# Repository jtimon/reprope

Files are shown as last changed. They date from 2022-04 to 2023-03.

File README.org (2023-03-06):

* Reprope

Reprope is a [[https://reprap.org/wiki/RepRap][reprap]] based on ropes or cables.

Cable based robotic designs are very scalable compared to other systems.

Depending on the needs, they can be configured for high precision and torque or high speed.

When it comes to leveraging cable usage for higher torque; Arquímedes himself said it quite clearly:

"Give me a place to stand, and I shall move the earth"

Some people told us Arquímedes once elevated a war ship with his own force
simply by using levers, pulleys, ropes and wooden stuff.

Anyway, it was just a joke, it can be removed with a commit.

* hangprinter

The reprope extends the hangprinter, with a special focus on adding
optional features like scaling it down, allowing squared printing
volumes, allowing extra anchors, allowing extra axes or even getting
use of those extra 3 90 degree axes to get tool chaning without an
extra servo, just rotate the head 90 degrees in 3 directions as you whish.

* Firmware

For now there is only work in progress firmware extending
reprap firmware (RRF) implementation of the hangprinter:

https://github.com/Duet3D/RepRapFirmware/pulls/jtimon

There may be some binaries in bin to test. But they shouldn't be
assumed to work on duet. Most of them will be compiled for the
stm32f4-wifi config on:

https://github.com/gloomyandy/RepRapFirmware

* Copyright

The copyright of this whole project belongs to the RepRope project developers.

The copyright for other free software and hardware projects this
depends on is described in theirr own projects.

This project is intended to be on free software licenses as light as
possible.

I will try to keep dependencies free.
In that sense, the hangprinter and reprap firmware seem to be
following free software licenses practices.

* License

All files included in this project are under MIT license (see [[./COPYING]]),

Currently some stl files used are not included in the project but
references to those files, because they have other licenses.

List of stl files that are used from external developers:

| Part                             | License                         | STL                                             | Notes                                                                                                |
|----------------------------------+---------------------------------+-------------------------------------------------+------------------------------------------------------------------------------------------------------|
| vslot t-nut adaptor for 3mm nuts | Creative Commons Non commercial | https://www.thingiverse.com/thing:3050607/files | You can also just buy regular commercial t-nuts, this is only cheaper if you're not going to sell it |

* NOTE: This is a work in progress, this printer doesn't work yet.

#+CAPTION: This is just the frame with the motors mounted with their reels
#+NAME:   fig:reprope-reels-only
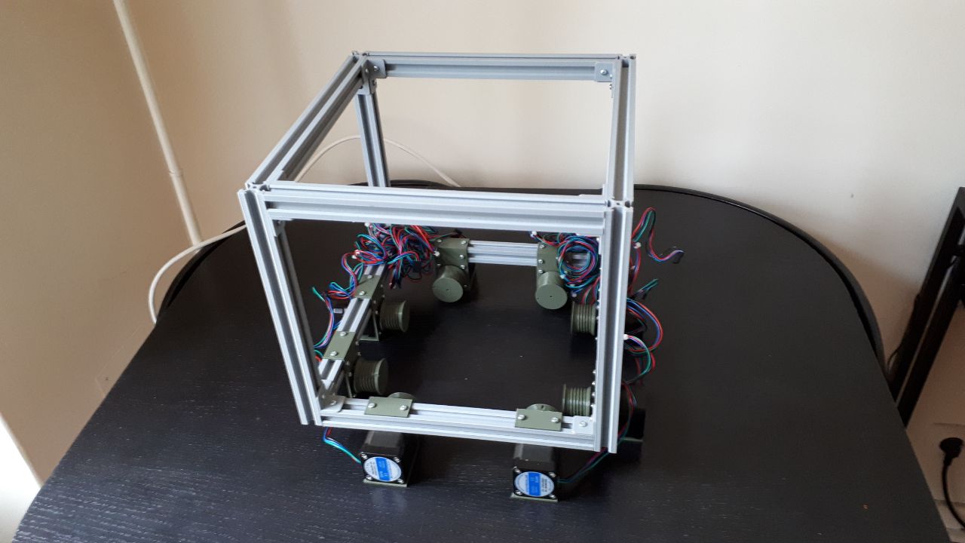
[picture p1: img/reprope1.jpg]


#+CAPTION: This is after adding the top pulleys too
#+NAME:   fig:reprope-pulleys-only
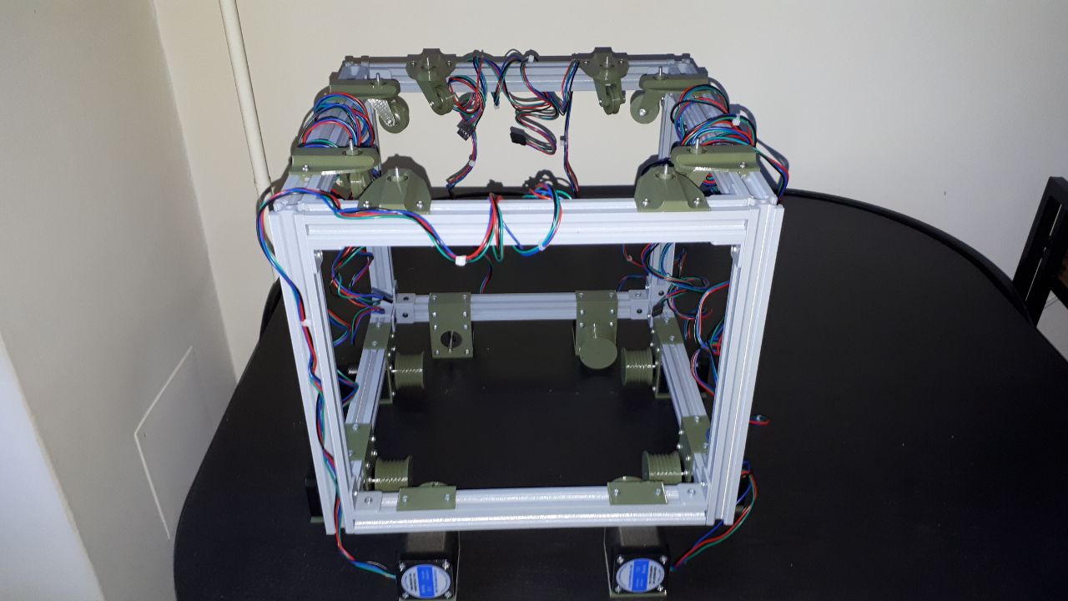
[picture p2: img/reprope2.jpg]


#+CAPTION: This is after adding some nylon ropes
#+NAME:   fig:reprope-blue-ropes
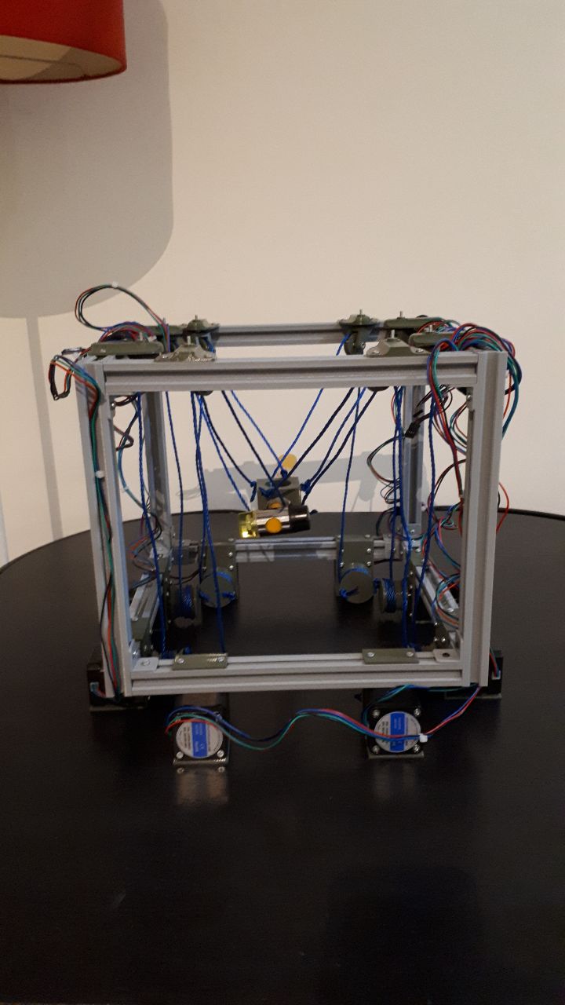
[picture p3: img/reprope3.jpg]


#+NAME:   fig:reprope-blue-ropes2
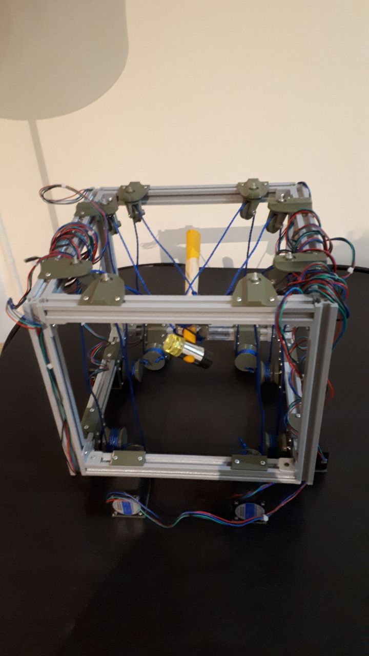
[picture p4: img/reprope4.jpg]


#+NAME:   fig:reprope-blue-ropes3
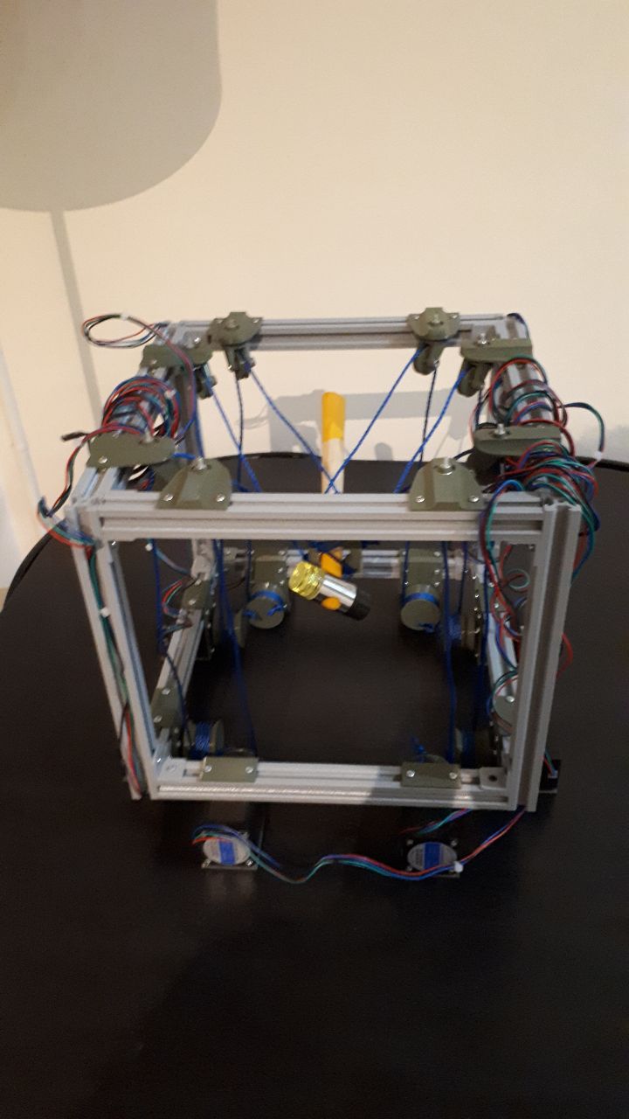
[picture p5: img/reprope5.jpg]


#+NAME:   fig:reprope-psu-box
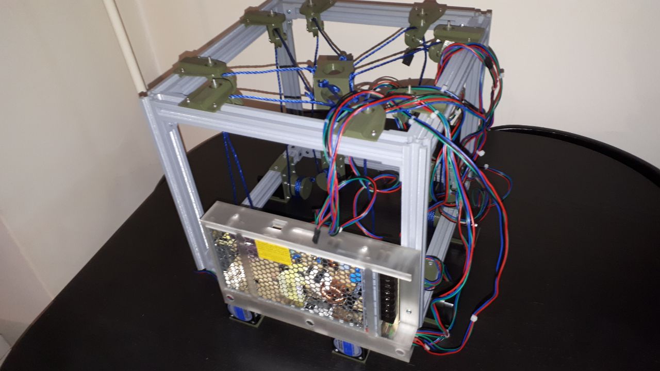
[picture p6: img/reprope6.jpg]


#+NAME:   fig:reprope-psu-box-cable-management
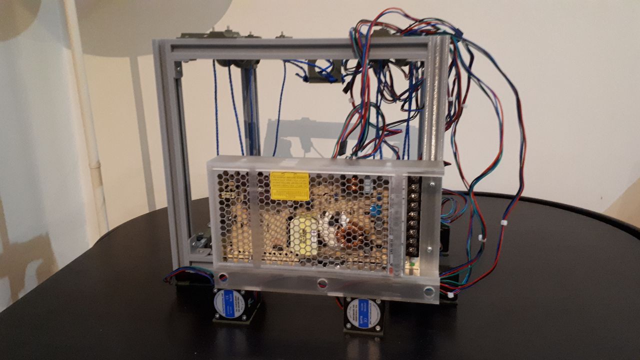
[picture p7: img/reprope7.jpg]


#+NAME:   fig:reprope-ac-in-corner
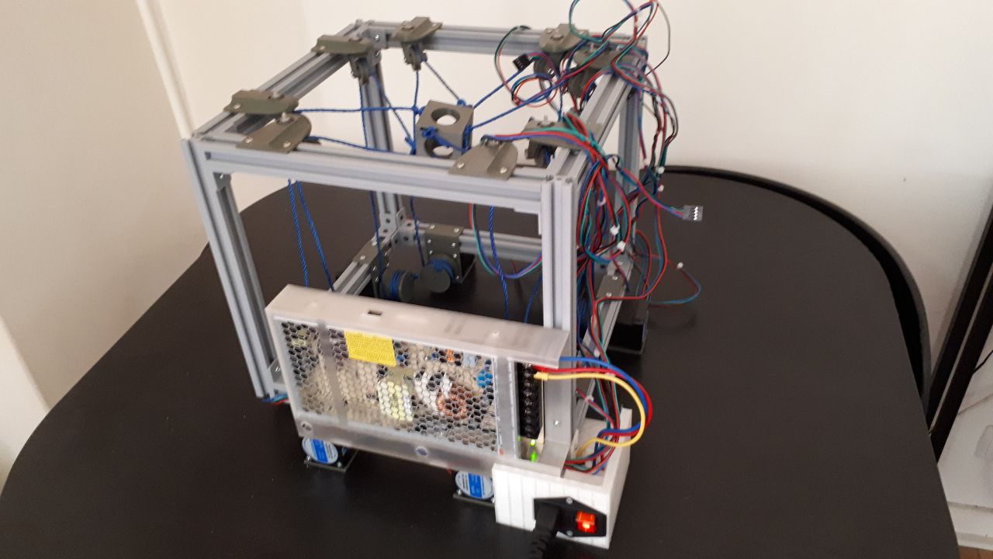
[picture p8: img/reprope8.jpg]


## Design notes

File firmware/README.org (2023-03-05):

* Firmware

Ideally, the reprope kynematics will be eventually supported in all three most popular free software 3d printing firmwares:

- [ ] Reprap firmware (RRF)
- [ ] Klipper
- [ ] Marlin

The plan is to implement, test and pull request them to their original repositories in that order.
A forked branch of the projects will be kept here as submodules and in github/jtimon with their respective names.
Ideally, in the end, a PR will be merged for each of the projects and the submodule can be erased here.

In the case of RRF, since I'm only going to test with non duet hardware for now, I'm not forking the original repository:

https://github.com/Duet3D/RepRapFirmware

but a different one that supports STM32F4 based boards such as the BTT octopus in the current BOM:

https://github.com/gloomyandy/RepRapFirmware

Still, the PR would be to the original repository, and only with the
reprope kynematic specific changes, so there will be a duet-reprope
branch and a stm32-reprope branch. The latter may stay here for a bit
longer until the gloomy version gets the next version including the
new kynematics.

* TODO [0/3] Firmwares
- [ ] Reprap Firmware (RRF)
- [ ] Klipper
- [ ] Marlin

* Why reprap firmware first?

Feel free to beat me to it in klipper.
Marlin I think is going to be harder because of the lack of
polymorphism, at least harder for me.
I may never do it in the case of marlin, quite honestly, but it would
be cool to have the new kynematics in all three.

It can be cheaper per unit using RRF because it doesn't strictly need
a raspbery pi, which are getting harder to get these days.
Besides, that's a whole linux system, many more things can go wrong
with that.

Whatever the order, I really want to do it for both RRF and klipper at
the very least. Sorry, Marlin just seems like too much work, at a glance.
Perhaps it's easier for somebody else who knows it better to port the
new kynematics, once it is done in other firmwares.
No warranties for anything anyway besides whatever gets done being
free software.

Another reason to do RRF first is that I can look at the tested and
working hangprinter kynematics implementation in there.
In my best hopes, once I port the reprope kynematics from RRF to
klipper, I will understand things enough to complete the port of the
hangprinter to klipper, which seems to be:

https://github.com/Klipper3d/klipper/blob/master/klippy/kinematics/winch.py

But, hey, it's well documented that some things are not implemented.

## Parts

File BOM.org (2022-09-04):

#+TODO: TODO WIP CAD PRINT LANG | DONE

* WIP first prototype sourcing

** 3d printed parts

| Part                                        | quantity | State | STL                                                       | CAD                          | Notes                                                                                              |
|---------------------------------------------+----------+-------+-----------------------------------------------------------+------------------------------+----------------------------------------------------------------------------------------------------|
| vslot t-nut adaptor for 3mm nuts (optional) |       77 | DONE  | https://www.thingiverse.com/thing:3050607/files           | MISSING                      | TODO: replace with a CAD parametric one, this one is creative commons but non-commercial           |
| Open builds-inspired 20x20 vslot 26cm       |       12 | DONE  | [[./STL/vslot2020-26cm.stl]]                                  | [[./CAD/vslot2020.FCStd]]        | TODO: parametrize with freeCAD so it isn't only 2020 vslot                                         |
| Corner bracket                              |       24 | DONE  | [[./STL/corner-bracket-20x20xM3.2.stl]]                       | [[./CAD/bracket.FCStd]]          | TODO: Parametrize in the same spreadshit as the extrusion one, for it only serves to unite corners |
| Motor mount                                 |        8 | DONE  | [[./STL/nema17-mount.stl]]                                    | [[./CAD/motor_mount_try1.FCStd]] |                                                                                                    |
| Reel                                        |        8 | DONE  | [[./STL/reel2-5rounds-5.4diam4.55flat.stl]]                   | [[./CAD/reel2.FCStd]]            | LANG: what is it? a reel or a spool? and in spanish?                                               |
| Pulley                                      |        8 | DONE  | [[./STL/pulleyB-Pulley4.stl]]                                 | [[./CAD/pulleyB.FCStd]]          |                                                                                                    |
| FixedSupport                                |        8 | DONE  | [[./STL/pulleyB-FixedSupport2.stl]]                           | [[./CAD/pulleyB.FCStd]]          |                                                                                                    |
| RotatingSupport                             |        8 | DONE  | [[./STL/pulleyB-RotatingSupport5.stl]]                        | [[./CAD/pulleyB.FCStd]]          |                                                                                                    |
| PSU Support                                 |        1 | DONE  | [[./STL/PSU_box-BoxBody2.stl]]                                | [[./CAD/PSU_box.FCStd]]          |                                                                                                    |
| Nut covers (optional)                       |     0-16 | DONE  | [[./STL/nut-tests-innerDiam3.4-NutWidth2.35-NutSize5.62.stl]] | [[./CAD/nut-tests.FCStd]]        | Just aesthetical anc convenient for a couple of nuts in the pulleys                                |
| Head moving Support                         |        1 | DONE  | [[./STL/head-v0.stl]]                                         | [[./CAD/head.FCStd]]             |                                                                                                    |
| Distance tool (optional)                    |      0-1 | DONE  | [[./STL/DistanceTool-Body.stl]]                               | [[./CAD/DistanceTool.FCStd]]     | Convenience tool to easily place the motors in place.                                              |
| AC In Corner                                |        1 | DONE  | [[./STL/AC-IN-plug-box-Body.stl]]                             | [[./CAD/AC-IN-plug-box.FCStd]]   | Require 1 insert, 3 bolts (TODO spec)                                                              |
| cable guide left                            |        1 | DONE  | [[./STL/cable_guide-Body.stl]]                                | [[./CAD/cable_guide.FCStd]]      |                                                                                                    |
| main box                                    |        1 | DONE  | [[./STL/reprope-BoxBody.stl]]                                 | [[./CAD/reprope.FCStd]]          |                                                                                                    |
| opctopus-like support                       |        1 | DONE  | [[./STL/reprope-BoardSupportBody.stl]]                        | [[./CAD/reprope.FCStd]]          |                                                                                                    |
| Down cable slide                            |        1 | DONE  | [[./STL/reprope-DownSlideBody.stl]]                           | [[./CAD/reprope.FCStd]]          |                                                                                                    |
| PSU cover                                   |        1 | DONE  | [[./STL/reprope-PSUCoverBody.stl]]                           | [[./CAD/reprope.FCStd]]          |                                                                                                    |

* (vitamins/printed/CNCed) Some of the parts can be done in metal too

| Part                                      | quantity | STL | CAD | Notes |
|-------------------------------------------+----------+-----+-----+-------|
| Open builds-aluminum 20x20 vslot XxYxZ cm |       12 |     |     |       |
| Corner brackets                           |       24 |     |     |       |
| t-nuts 3 mm diameter (for 2020 v/t-slot)  |       77 |     |     |       |

** vitamins (parts that cannot be 3d printed, in reprap jargon)

| name                                    | model                       | brand         | units | price (unit) | price (total) | unit | Sourcing                                                                       |
|-----------------------------------------+-----------------------------+---------------+-------+--------------+---------------+------+--------------------------------------------------------------------------------|
| stepper motors (x8)                     | 17HS19-2004S1 NEMA 17       | StepperOnline |    10 |       10.164 |        101.64 | eur  | https://www.amazon.es/gp/product/B07CPQC1Y6/ref=ppx_yo_dt_b_asin_title_o09_s00 |
| stepper motor controllers (x8)          | TMC2209 V2.0                | TMC           |    10 |        6.996 |         69.96 | eur  | https://www.amazon.es/gp/product/B085WZYK1T/ref=ppx_yo_dt_b_asin_title_o07_s00 |
| main board                              | STM32F429ZGT6 (Octopus Pro) | BIGTREETECH   |     1 |        92.99 |         92.99 | eur  | https://www.amazon.es/gp/product/B09JC2NR1L/ref=ppx_yo_dt_b_asin_title_o07_s01 |
| Power Source Unit (PSU)                 | LRS-200-24                  | MEANWELL      |     1 |        19.86 |         19.86 | eur  | https://www.amazon.es/gp/product/B07F29RHNP/ref=ppx_yo_dt_b_asin_title_o03_s01 |
| bearings 633z (3mm x 13mm x 5 mm) (x16) | 633z (3mm x 13mm x 5 mm)    |               |    20 |        1.372 |         27.44 | eur  | https://www.makerbeam.com/makerbeam-bearings-10p-for-makerbeam.html            |
| wifi board                              | ESP8266 WiFi                | BIGTREETECH   |     1 |        10.25 |         10.25 | eur  | https://biqu.equipment/products/bigtreetech-esp8266                            |
|-----------------------------------------+-----------------------------+---------------+-------+--------------+---------------+------+--------------------------------------------------------------------------------|
| Total                                   |                             |               |       |              |        322.14 | eur  |                                                                                |
#+TBLFM: $6=$4*$5::@>$6=vsum(@2$6..@-1$6)

** Vitamins cheap/quantity

If you find one provider, he will be happy to sell you more of thse, how many do you need, again?

| name                                | model                | brand | units | price (unit) | price (total) | unit | Sourcing                                                                       |
|-------------------------------------+----------------------+-------+-------+--------------+---------------+------+--------------------------------------------------------------------------------|
| M3 screws 8 mm                      |                      |       |    61 |              |             0 |      | https://www.amazon.es/gp/product/B07FL4G1DZ/ref=ppx_yo_dt_b_asin_title_o03_s01 |
| M3 screws 5 mm                      |                      |       |    32 |              |             0 |      |                                                                                |
| M3 screws 14 mm                     |                      |       |       |              |             0 |      | https://www.amazon.es/gp/product/B01AXUS4JU/ref=ppx_yo_dt_b_asin_title_o01_s02 |
| M4 screws 12 mm  (could be shorter) |                      |       |     2 |              |               |      |                                                                                |
| M4 screws x mm  (optional)          |                      |       |     2 |              |               |      | TODO find out how short the M4 screws on the top of the PSU must be            |
| Cables and connectors               | various TODO specify |       |       |              |             0 | eur  |                                                                                |
| Tools                               | various TODO specify |       |       |              |             0 | eur  |                                                                                |
|-------------------------------------+----------------------+-------+-------+--------------+---------------+------+--------------------------------------------------------------------------------|
| Total                               |                      |       |       |              |             0 | eur  |                                                                                |
#+TBLFM: $6=$4*$5::@>$6=vsum(@2$6..@-1$6)

REM spectra and dyneema lines

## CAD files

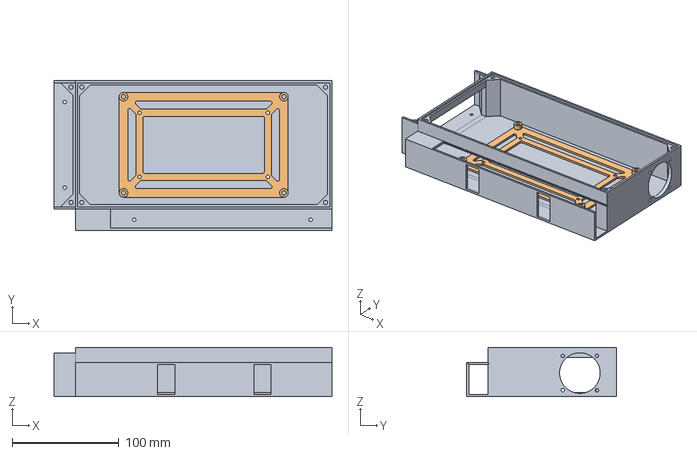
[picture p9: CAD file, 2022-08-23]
CAD/reprope.FCStd
260.0 x 140.0 x 46.0 mm
BoxBody
BoardSupportBody

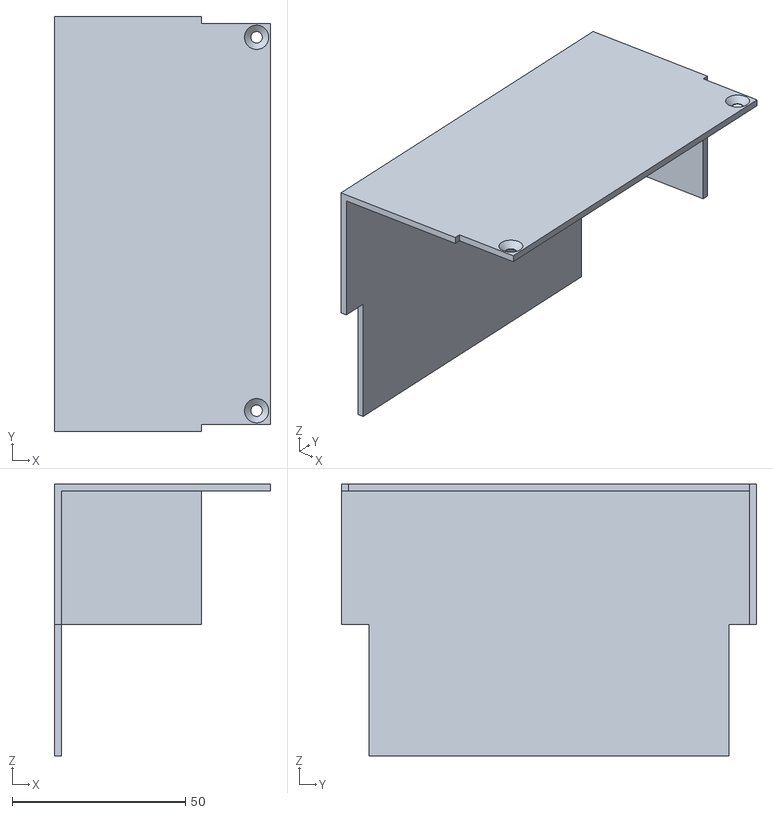
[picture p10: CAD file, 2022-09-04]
STL/new_box0-PSUCoverBody.stl
62.5 x 120.0 x 78.6

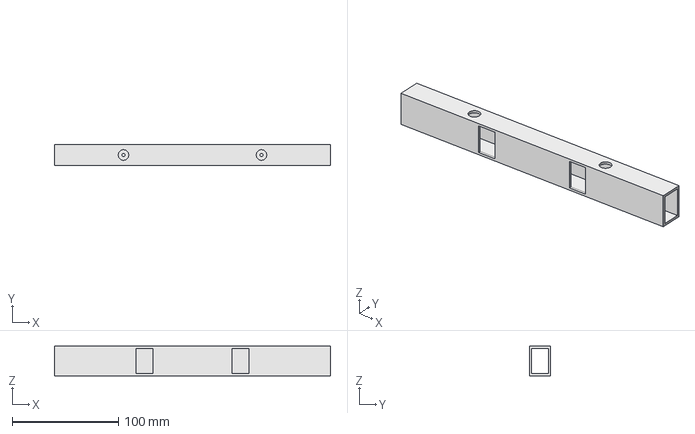
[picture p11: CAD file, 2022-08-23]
CAD/cable_guide.FCStd
260.0 x 20.0 x 28.0 mm

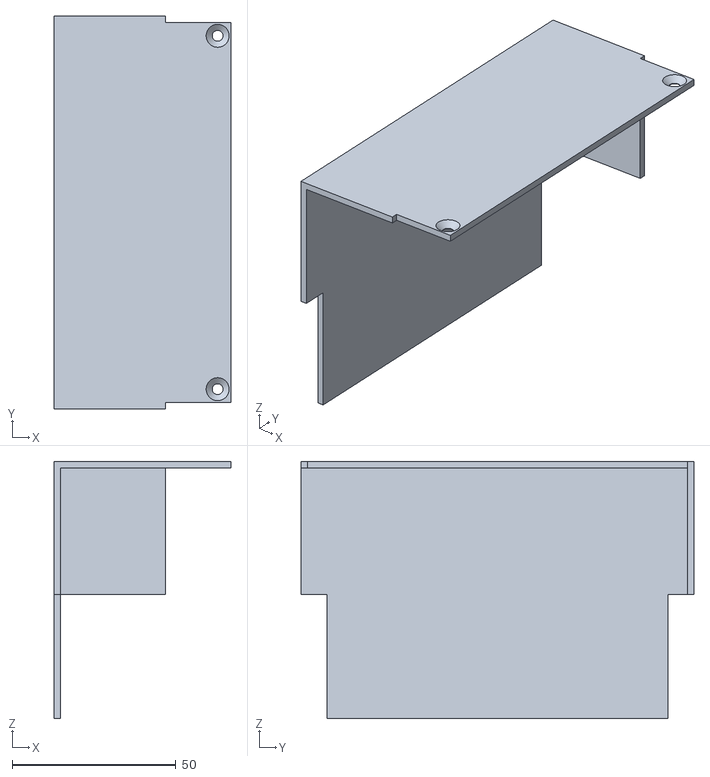
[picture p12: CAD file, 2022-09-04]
STL/reprope-PSUCoverBody.stl
54.0 x 120.0 x 78.6

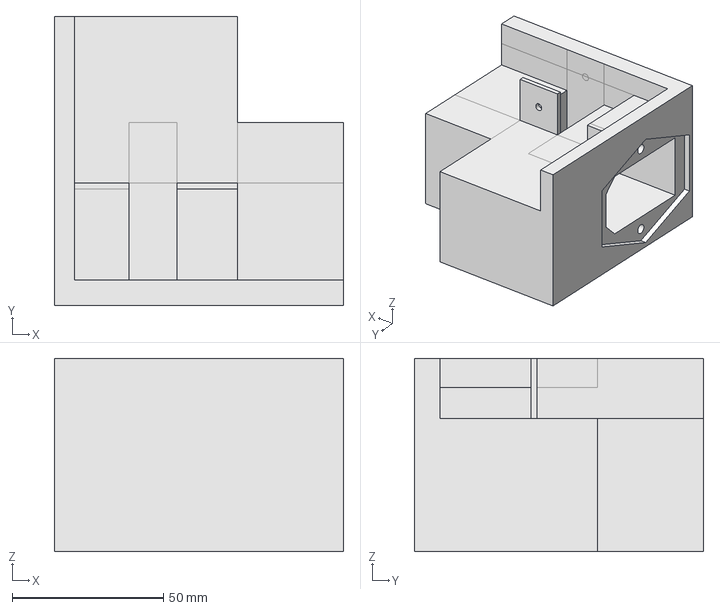
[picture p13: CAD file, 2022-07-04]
CAD/AC-IN-plug-box.FCStd
95.6 x 95.6 x 64.0 mm

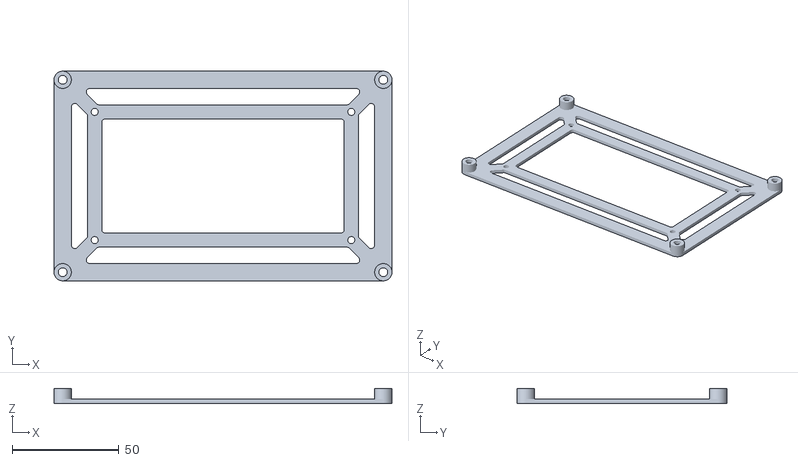
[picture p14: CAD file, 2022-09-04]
STL/reprope-BoardSupportBody.stl
158.1 x 98.1 x 7.00

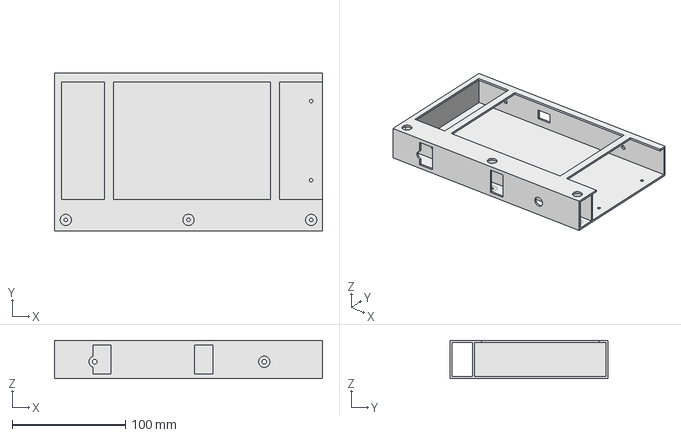
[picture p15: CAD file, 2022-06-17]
CAD/PSU_box.FCStd
237.0 x 140.0 x 34.0 mm

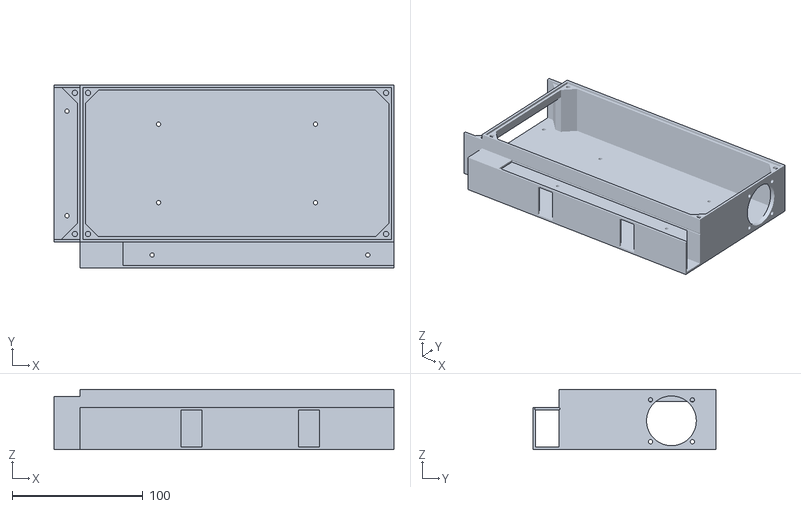
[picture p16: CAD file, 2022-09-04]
STL/reprope-BoxBody.stl
260.0 x 140.0 x 46.0

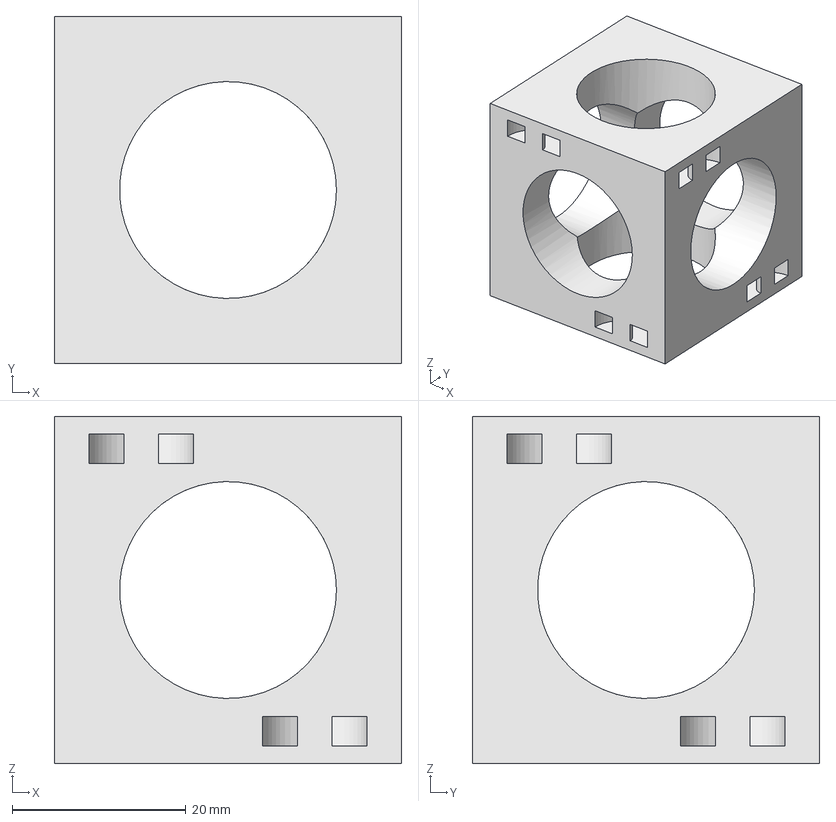
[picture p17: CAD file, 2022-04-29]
CAD/head.FCStd
40.0 x 40.0 x 40.0 mm

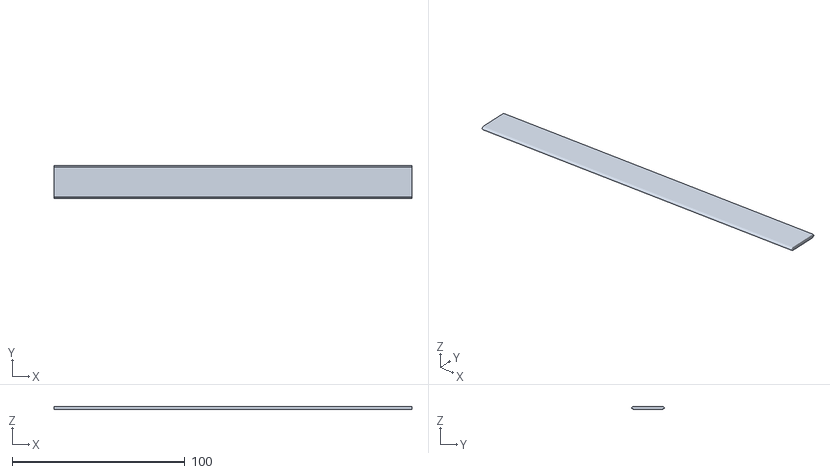
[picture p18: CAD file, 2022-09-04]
STL/reprope-DownSlideBody.stl
207.0 x 19.2 x 2.00

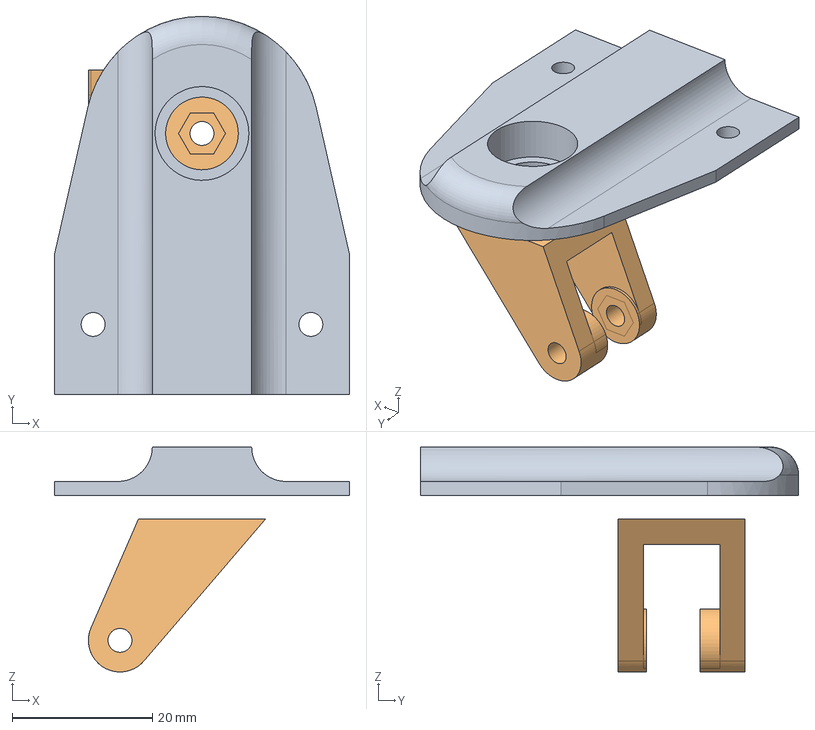
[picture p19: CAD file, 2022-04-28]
CAD/pulleyB.FCStd
42.0 x 53.9 x 32.0 mm
FixedSupportBody
RotatingSupport

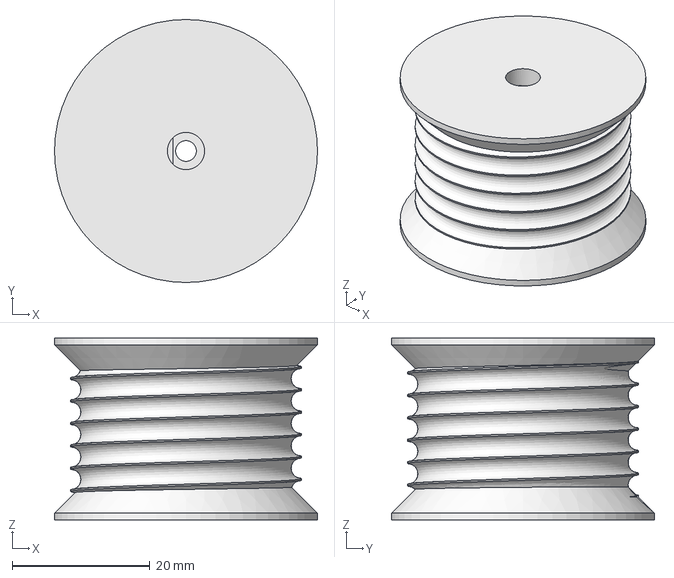
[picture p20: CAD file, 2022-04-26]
CAD/reel2.FCStd
38.1 x 38.1 x 26.4 mm

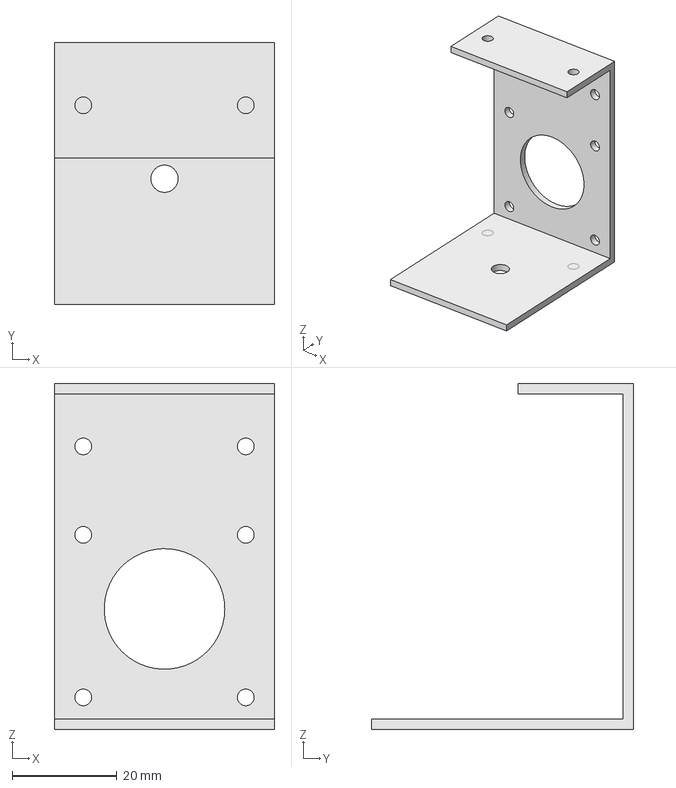
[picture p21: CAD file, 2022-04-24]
CAD/motor_mount_try1.FCStd
42.0 x 50.0 x 66.0 mm

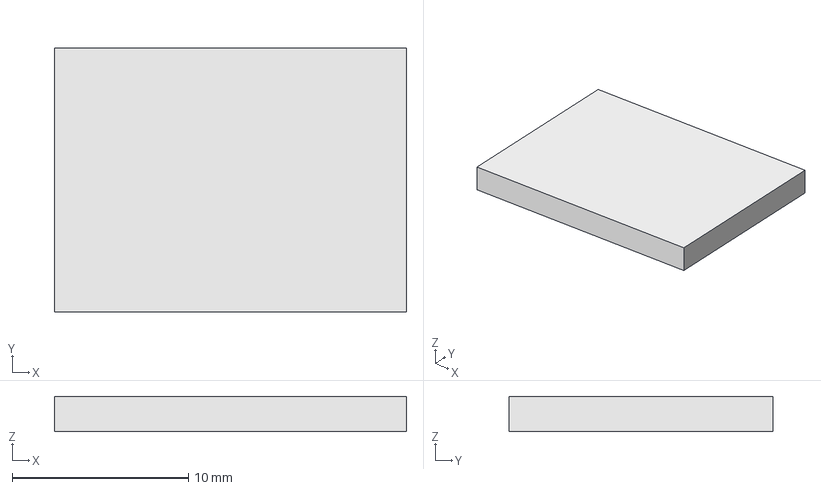
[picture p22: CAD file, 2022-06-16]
STL/DistanceTool.FCStd
20.0 x 15.0 x 2.00 mm

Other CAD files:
STL/cable_guide-Body.stl
STL/AC-IN-plug-box-Body.stl
STL/PSU_box-BoxBody2.stl
CAD/vslot2020.FCStd
CAD/bracket.FCStd
CAD/nut-tests.FCStd
STL/DistanceTool-Body.stl
STL/corner-bracket-20x20xM3.2.stl
STL/head-v0.stl
STL/nema17-mount.stl
STL/nut-tests-innerDiam3.4-NutWidth2.35-NutSize5.62.stl
STL/pulleyB-FixedSupport2.stl
STL/pulleyB-Pulley4.stl
STL/pulleyB-RotatingSupport5.stl
STL/reel2-5rounds-5.4diam4.55flat.stl
STL/vslot2020-26cm.stl

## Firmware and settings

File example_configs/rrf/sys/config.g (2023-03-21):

; Configuration file for BTT Octopus Pro v1.0 F429 (firmware version 3)
; executed by the firmware on start-up
;
; generated by RepRapFirmware Configuration Tool v3.4.0-LPC-STM32+4 on Mon Aug 29 2022 21:37:15 GMT+0100 (Western European Summer Time)

; General preferences
G90                                           ; send absolute coordinates...
M83                                           ; ...but relative extruder moves
M550 P"reprope"                               ; set printer name

; Network
M552 S1                                       ; enable network
M586 P0 S1                                    ; enable HTTP
M586 P1 S0                                    ; disable FTP
M586 P2 S0                                    ; disable Telnet

; Logging
M929 P"log.txt" S0 ; start logging to file eventlog.txt

; Axis and motor configuration (example hangprinter config)
; M569 P0 S1 ; drive 0 (X motor output aka A) goes forwards
; M569 P1 S1 ; drive 1 (Y motor output aka B) goes forwards
; M569 P2 S1 ; drive 2 (Z motor output aka C) goes forwards
; M569 P3 S1 ; drive 3 (extruder) goes forwards
; M569 P4 S1 ; drive 4 (E1 motor output aka U aka D) goes forwards
; M584 X0 Y1 Z2 E3 U4 ; create U axis for the D motor, attached to the E1 motor connector
; M669 K6 A0.0:-2163.0:-75.5 B-1841.0:741.0:-75.5 C1639.0:1404.0:-75.5 D0:0:3250.5 P1500 ; set Hangprinter kinematics parameters
; M92 X101.86 Y101.86 Z101.85 U101.86 ; set steps/mm for each spool
; M208 S0 Z1500 ; maximum height 1500mm
; M208 S1 Z-5 ; minimum height -5mm
; M203 X6000 Y6000 Z6000 E3600 ; maximum linear speeds mm/minute
; M906 X1000 Y1000 Y1000 E1000 ; set motor currents (mA)

; Drives
M569 P0 S0 D3 V40                             ; physical drive 0 goes backwards using TMC2209 driver timings (Stealthchop)
M569 P1 S0 D3 V40                             ; physical drive 1 goes backwards using TMC2209 driver timings (Stealthchop)
M569 P2 S0 D3 V40                             ; physical drive 2 goes backwards using TMC2209 driver timings (Stealthchop)
M569 P3 S0 D3 V40                             ; physical drive 3 goes backwards using TMC2209 driver timings (Stealthchop)
M569 P4 S0 D3 V40                             ; physical drive 4 goes backwards using TMC2209 driver timings (Stealthchop)
M569 P5 S0 D3 V40                             ; physical drive 5 goes backwards using TMC2209 driver timings (Stealthchop)
M569 P6 S0 D3 V40                             ; physical drive 6 goes backwards using TMC2209 driver timings (Stealthchop)
; M569 P7 S0 D3 V40                             ; physical drive 7 goes backwards using TMC2209 driver timings (Stealthchop)
; M584 X0 Y1 Z2 U3 V4 W5 A6 B7 R0               ; set drive mapping

; set Hangprinter kinematics parameters
; M669 K6 N8 A-115.0:74.0:250.0 B-74.0:115.0:250.0 C74.0:115.0:250.0 D115.0:74.0:250.0 E115.0:-74.0:250.0 F74.0:-115.0:250.0 G-74.0:-115.0:250.0 H-115.0:-74.0:250.0 P100
; M669 K6 N6 A-115.0:74.0:250.0 B-74.0:115.0:250.0 C74.0:115.0:250.0 D115.0:74.0:250.0 E115.0:-74.0:250.0 F74.0:-115.0:250.0 P100
; M669 K6 N7 A-115.0:74.0:250.0 B-74.0:115.0:250.0 C74.0:115.0:250.0 D115.0:74.0:250.0 E115.0:-74.0:250.0 F74.0:-115.0:250.0 H-74.0:-115.0:250.0 P100

; Reprope setup 8 anchors:
; M669 K6 N9 A-115.0:74.0:250.0 B-74.0:115.0:250.0 C74.0:115.0:250.0 D115.0:74.0:250.0 E115.0:-74.0:250.0 F74.0:-115.0:250.0 H-74.0:-115.0:250.0 I-115.0:-74.0:250.0 P100
; M666 Q0.007 R15.0:15.0:15.0:15.0:15.0:15.0:15.0:15.0 U2:2:2:2:2:2:2:2 O1:1:1:1:1:1:1:1 L20:20:20:20:20:20:20:20 H255:255:255:255:255:255:255:255 H25:25:25:25:25:25:25:25
; M584 X0 Y1 Z2 U3 V4 W5 A6 B7 R0               ; set drive mapping

; Reprope setup 4 anchors:
M584 X0 Y2 Z4 U6 R0               ; set drive mapping
M669 K6 N4 A-115.0:74.0:250.0 B74.0:115.0:250.0 C115.0:-74.0:250.0 D-74.0:-115.0:250.0 P100
M666 A2 Q0.007 R15.0:15.0:15.0:15.0 U2:2:2:2 O1:1:1:1 L20:20:20:20 H255:255:255:255 H25:25:25:25
M350 X16 Y16 Z16 I1       ; configure 1/16 microstepping with interpolation
M92 X80 Y80 Z80 U80 ; set steps per mm
M566 X900.00 Y900.00 Z900.00 U900.00 ; set maximum instantaneous speed changes (mm/min)
M203 X18000.00 Y18000.00 Z18000.00 U18000.00 ; set maximum speeds (mm/min)
M201 X2000.00 Y2000.00 Z2000.00 U2000.00 ; set accelerations (mm/s^2)
; M906 X800 Y800 Z800 U800 I30                  ; set motor currents (mA) and motor idle factor in per cent
; M906 X1200 Y1200 Z1200 U1200    ; set motor currents (mA)
M906 I30                        ; Idle current percentage

M204 P1500 T2000 ; Set printing acceleration and travel accelerations

; M350 X16 Y16 Z16 U16 V16 W16 A16 B16 I1       ; configure microstepping with interpolation
; M350 X16 Y16 Z16 I1       ; configure 1/16 microstepping with interpolation

; pi * 30 / 200 = length_per_step = pi * spool_diameter / steps_per_motor_rev = 0.47123889803
; TODO adapt parameters to reprope kynematics
; M92 X80 Y80 Z80 U80 V80 W80 A80 B80 ; set steps per mm
; M92 X80 Y80 Z80 ; set steps per mm
; M566 X900.00 Y900.00 Z900.00 U900.00 V900.00 W900.00 A900.00 B900.00 ; set maximum instantaneous speed changes (mm/min)
; M203 X6000.00 Y6000.00 Z6000.00 U6000.00 V6000.00 W6000.00 A6000.00 B6000.00 ; set maximum speeds (mm/min)
; M201 X500.00 Y500.00 Z500.00 A500.00 B500.00 C500.00 D500.00 U500.00 ; set accelerations (mm/s^2)
; M204 P500 T2000 ; Set printing acceleration and travel accelerations
; M906 X800 Y800 Z800 U800 V800 W800 A800 B800 I30                  ; set motor currents (mA) and motor idle factor in per cent
; M906 X800 Y800 Z800 I30                  ; set motor currents (mA) and motor idle factor in per cent
; M84 S30                                       ; Set idle timeout

; Axis Limits
; M208 X0 Y0 Z0 S1                              ; set axis minima
; M208 X230 Y210 Z200 S0                        ; set axis maxima
; M208 Z-4 S1                              ; set axis minima
; M208 Z200 S0                        ; set axis maxima

; Endstops
; M915 P0:1:2:3:4:5:6:7 S-127 H10 R1 ; Set very sensible of stall detect
; M915 P0:1:2:3:4:5:6:7 S40 H10 R1 ; Set very sensible of stall detect
; M574 X1 S3                                    ; configure sensorless endstop for low end on X
; M574 Y1 S3                                    ; configure sensorless endstop for low end on Y
; M574 Z1 S3                                    ; configure sensorless endstop for low end on Z
; M574 U1 S3                                    ; configure sensorless endstop for low end on U
; M574 V1 S3                                    ; configure sensorless endstop for low end on V
; M574 W1 S3                                    ; configure sensorless endstop for low end on W
; M574 A1 S3                                    ; configure sensorless endstop for low end on A
; M574 B1 S3                                    ; configure sensorless endstop for low end on B

; M574 Y1 S1 P"ystop"                           ; configure switch-type (e.g. microswitch) endstop for low end on Y via pin ystop
; M574 Z1 S2                                    ; configure Z-probe endstop for low end on Z

; Z-Probe
; M950 S0 C"servo0"                             ; create servo pin 0 for BLTouch
; M558 P9 C"^probe" H5 F120 T6000               ; set Z probe type to bltouch and the dive height + speeds
; G31 P500 X0 Y0 Z2.5                           ; set Z probe trigger value, offset and trigger height
; M557 X15:215 Y15:195 S20                      ; define mesh grid

; Heaters
; M140 H-1                                      ; disable heated bed (overrides default heater mapping)
; M308 S0 P"e0temp" Y"thermistor" T100000 B4092 ; configure sensor 0 as thermistor on pin e0temp
; M950 H0 C"e0heat" T0                          ; create nozzle heater output on e0heat and map it to sensor 0
; M307 H0 B0 S1.00                              ; disable bang-bang mode for heater  and set PWM limit
; M143 H0 S120                                  ; set temperature limit for heater 0 to 120C

; Fans
; M950 F0 C"fan0" Q500                          ; create fan 0 on pin fan0 and set its frequency
; M106 P0 S0 H T45                              ; set fan 0 value. Thermostatic control is turned on

; Tools
; M563 P0 D0 F0                                 ; define tool 0
; G10 P0 X0 Y0 Z0                               ; set tool 0 axis offsets
; G10 P0 R0 S0                                  ; set initial tool 0 active and standby temperatures to 0C

; Custom settings are not defined

; Miscellaneous
; M575 P1 S2 B57600                             ; enable support for tft

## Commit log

2022-04-24 CAD: Extrusion and 90-bracket
    [bracket.FCStd, vslot2020.FCStd]
2022-04-24 CAD: initial motor mount
    [motor_mount_try1.FCStd]
2022-04-24 CAD: initial reel (x8), print: reelx8
    [reel2.FCStd]
2022-04-25 BOM: initial pieces
    [corner-bracket-20x20xM3.2.stl, nema17-mount.stl, reel2-5rounds-5.4diam4.55flat.stl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]
2022-04-25 WIP: CAD: Pulley with support
    [pulleyB.FCStd]
2022-04-25 CAD: wip: rotating support internal nuts
    [pulleyB.FCStd]
2022-04-25 CAD: changes to pulley
    [pulleyB.FCStd]
2022-04-25 CAD: More changes to pulley
    [pulleyB.FCStd]
2022-04-25 cad: pulley: add nuts
    [pulleyB.FCStd]
2022-04-25 cad: pulley: top nut
    [pulleyB.FCStd]
2022-04-25 pulley fix
    [pulleyB.FCStd]
2022-04-25 cad: pulley: top support
    [pulleyB.FCStd]
2022-04-25 pulley recovery
    [pulleyB.FCStd]
2022-04-25 more bearing width 5 -> 5.2
    [pulleyB.FCStd]
2022-04-25 RotatingSupportArcBorder 3 -> 3.2
    [pulleyB.FCStd]
2022-04-25 RotatingSupportArcBorder 3.2 -> 3
    [pulleyB.FCStd]
2022-04-25 More detailed inner pocket so that the inner nuts are fully covered
    [pulleyB.FCStd]
2022-04-25 CAD: "Final" pulley (just the wheel)
    [pulleyB-Pulley4.stl, pulleyB.FCStd]
2022-04-26 cad: pulley: Rename TopBearingPocket
    [pulleyB.FCStd]
2022-04-26 cad: pulley: bugfix: One of the two internal nuts cannot be fixed in angle
    If you try to have both nuts on the same angle, things will break
    because the threating wants them to put them in different angles to
    fix the bearing.
    [pulleyB.FCStd]
2022-04-26 cad: pulley: PulleyLateralClearance 3 -> 2
    [pulleyB.FCStd]
2022-04-26 cad: reel: spreadsheet: Calculate PulleyCenterDistanceFromExtrussion for pulley
    REM: Unify files or at least spreadsheets
    [reel2.FCStd]
2022-04-26 cad: pulley: CenterDistanceFromExtrussion 17 -> 17.19
    [pulleyB.FCStd]
2022-04-26 cad: pulley: NutSizeToSize 5.62 -> 5.7
    [pulleyB.FCStd]
2022-04-26 cad: pulley: rotating: top nut: put nut on the other side of the top
    ie on the top side of the top, if that makes sense.
    [pulleyB.FCStd]
2022-04-26 cad: pulley: ratating: effectively disable external nut
    [pulleyB.FCStd]
2022-04-26 fixup: cad: pulley: ratating: effectively disable external nut
    [pulleyB.FCStd]
2022-04-26 cad: pulley: NutSizeToSize 5.7 -> 5.8
    [pulleyB.FCStd]
2022-04-26 cad: rotating: PulleyLateralClearance=2
    [pulleyB.FCStd]
2022-04-26 cad: pulley: Make ClearanceBetweenSupports parametric
    [pulleyB.FCStd]
2022-04-26 cad: FixedSupport: Use tangent for conecting with the arc
    [pulleyB.FCStd]
2022-04-26 BOM: STL: Add rotating support, make links to files
    The bearings are the makerbeam ones, but find the specs outside of that little pack
    [pulleyB-RotatingSupport5.stl]
2022-04-26 cad: fixed support: make it taller so that the bearing doesn't move
    And
    - Add a pocket so that the screws don't have to be longer
    - Add a filet at the end mainly for aesthetics, but also for saving a bit of material, perhaps
    [pulleyB.FCStd]
2022-04-28 cad: pulley: unknown change if any
    probably just looking around the sketches
    [pulleyB.FCStd]
2022-04-28 BOM: STL: Add fixed support model
    [pulleyB-FixedSupport2.stl]
2022-04-28 CAD: POM: STL: Add nut optional covers
    [nut-tests-innerDiam3.4-NutWidth2.35-NutSize5.62.stl, nut-tests.FCStd]
2022-04-29 Doc: Add some images with the current progress
2022-04-29 CAD: STL: Head: Head v0 (just for movement testing, tool mounting mechanism yet)
    [head-v0.stl, head.FCStd]
2022-05-02 img: Add more protoype images with headV0 and cheap plastic ropes
    There's literally a tool mounted on the head, as promissed in the
    previous commit [ie CAD: STL: Head: Head v0 (just for movement
    testing, tool mounting mechanism yet)].
    An extruder would be better, but we're just not there yet.
    Note: make the hole in the spool bigger
    proposed name for the new param: RopeHoleClearance
2022-05-04 BOM: Improve vitamins, calculate total
2022-05-04 vitamin_specs: Add Octopus_Pro - beta.stp for CAD
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2022-06-16 CAD: STL: BOM: Add optional "distance tool" to place motors properly easily
    [DistanceTool-Body.stl, DistanceTool.FCStd]
2022-06-16 POM: Vitamins: Upgrade PSU to 24v meanwell 200w
2022-06-16 CAD: STL: BOM: Add PSU support/box
    [PSU_box-BoxBody.stl, PSU_box.FCStd]
2022-06-17 Fix PSU box (untested)
    [PSU_box-BoxBody.stl, PSU_box-BoxBody2.stl, PSU_box.FCStd]
2022-07-04 CAD: STL: Corner for AC In plug
    [AC-IN-plug-box-Body.stl, AC-IN-plug-box.FCStd]
2022-08-23 Introduce cable guided
    [cable_guide-Body.stl, cable_guide.FCStd]
2022-08-23 CAD: Introduce reprope CAD file with several bodies, including a box for a board
    [reprope.FCStd]
2022-08-24 simulator: refactor: introduce plot_cube_data and use it for the frame
2022-08-24 simulator: Add centered nozzle
2022-08-25 simulator: unify had and nozzle in the same plot function
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2022-08-30 Config: RRF: initial generated config
    [bed.g, config.g, deployprobe.g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]
2022-08-30 config: RRF: board.txt: configure Diag Pins for all 8 drivers
2022-08-30 config: RRF: config.g: configure all 8 drives with Stealthchop and stall guard
    [config.g]
2022-08-30 config: RRF: Temporary: fake homing for now
    [homeall.g, homex.g, homey.g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]
2022-09-04 BOM: STL: commit the parts that are already printed
    Even though they may not be perfect yet
    [reprope-BoardSupportBody.stl, reprope-BoxBody.stl, reprope-DownSlideBody.stl]
2022-09-04 CAD: reprope: Fix PSU cover
    [reprope-PSUCoverBody.stl]
2022-09-04 BOM: STL: Add PSU cover
    [new_box0-PSUCoverBody.stl]
2022-09-12 config: RRF: Seemingly working config for hangprinter
    [config.g, homeall.g]
2022-09-12 config: RRF: Add a couple of testing macros for convenience
    [8_motors_test.g, basic_test.g]
2022-12-17 WIP: changes in config
    [config.g]
2023-03-05 RRF: config: All 8 motors backwards
    [config.g]
2023-03-06 config: fix: there was a mix of 9 anchiors and 8 in the config
    [config.g]
2023-03-14 HP: 4AT: A config that works for 4 all-top anchors
    [config.g]
2023-03-14 Config: 4 on top fast test
    [test_rr_4top.g]
2023-03-21 Firmware: Config: Adapt to #603 on rrf
    firmware-stm32f4-wifi-v3.5-hangprinter-allow-prism-a43f7b37.bin
    [config.g, test_rr_4top.g]
